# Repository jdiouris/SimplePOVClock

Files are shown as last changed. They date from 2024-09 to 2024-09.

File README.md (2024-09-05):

# Horloge à persistance rétinienne
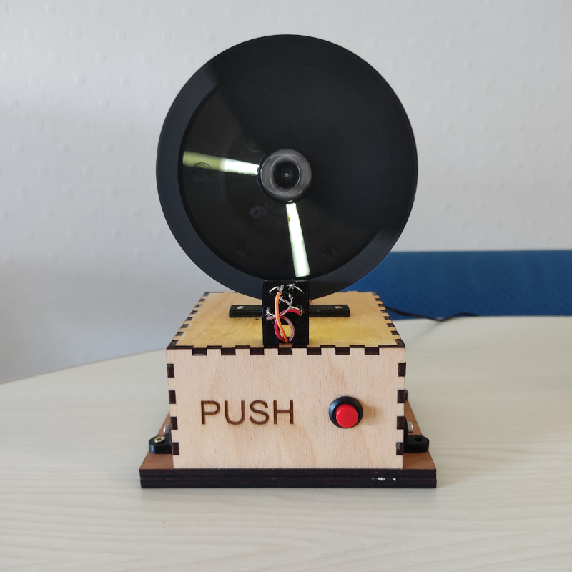
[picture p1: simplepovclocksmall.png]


## Principe
Un disque muni d'une fente tourne sur son axe. Des leds s'allument périodiquement pour visualiser les aiguilles des heures et des minutes. Un bouton poussoir permet de démarrer la rotation ou l'arrêt du disque. Deux boutons poussoirs à l'arrière permettent de régler l'heure et les minutes. L'heure est sauvegardée dans un circuit RTC.

##  Mécanique
Le boitier et le socle sont en contreplaqué 5mm découpé au laser. Les autres pièces sont réalisées en impression 3D.

|Pièce | Fichier source | Fichier de fabrication |
| ---- | --- | --- |
| Boitier | box.lbrn2  | box.dxf |
| Socle (2) | socle.lbrn2  | socle.dxf |
 | Coupelle | coupelle.scad | coupelle.stl |
| Disque | screen3.scad | screen3.stl |
|Support coupelle | supmoteur.scad | sup1.stl |
|Support coupelle | supmoteur.scad | sup2.stl |
|Support coupelle | supmoteur.scad | sup3.stl |
| Support CNY70 | cny70.scad | cny70.stl |
| Attache boite au socle (4) | attache.scad | attache.stl |

## Electronique

Les composants suivants :

| Composant | Quantité |
| --- | --- |
| Arduino uno | 1 |
| CNY70 | 1 |
| BD139 | 2 |
 | MOSFET | 1 |
 |Module horloge DS1302 | 1 |
 |LEDS 10 mm haute luminosité| 10 |
 | Diode 1N4148 | 1 |
 | Condensateur 10uF | 1|
 | Résistances | voir schéma |
 | Boutons poussoirs diamêtre 12.5 mm | 3 |

 Le schéma est détaillé dans le fichier schema.pdf. La pluspart des composants sont montés sur une carte de prototypage shield Arduino. Le capteur optique CNY70 est monté sur le support imprimé en 3d avec les deux résistances associées.

 ## Programme
 Le programme arduino est povc2.ino.

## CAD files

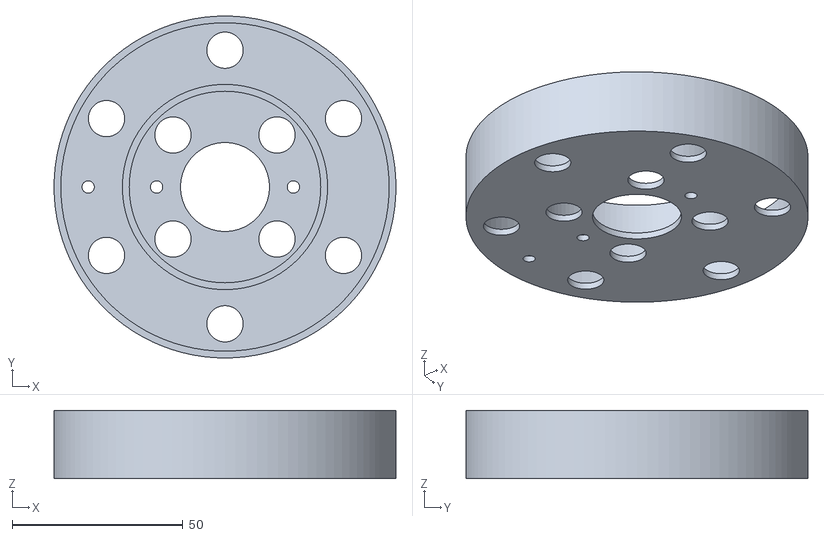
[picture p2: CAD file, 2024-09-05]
coupelle.stl
100.0 x 100.0 x 20.0

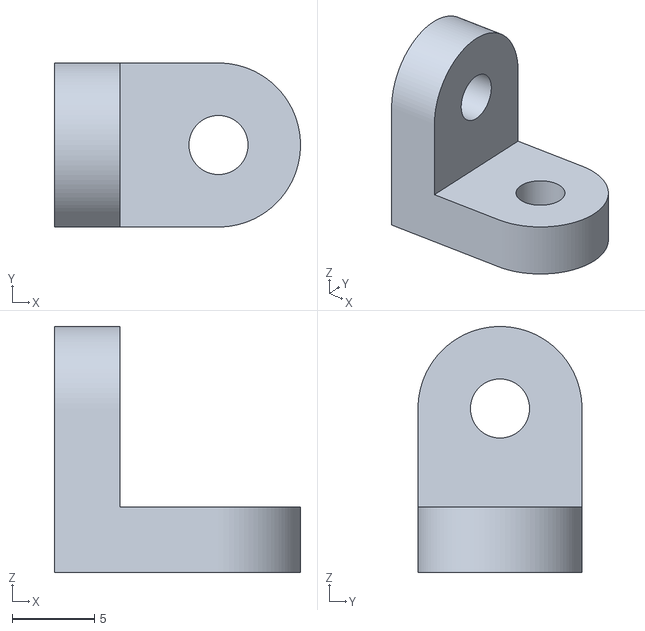
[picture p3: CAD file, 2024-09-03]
attache.stl
15.0 x 10.0 x 15.0

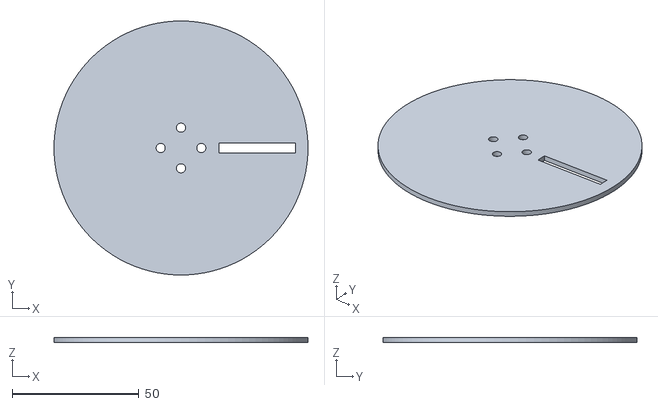
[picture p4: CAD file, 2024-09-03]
screen3.stl
100.0 x 100.0 x 2.00

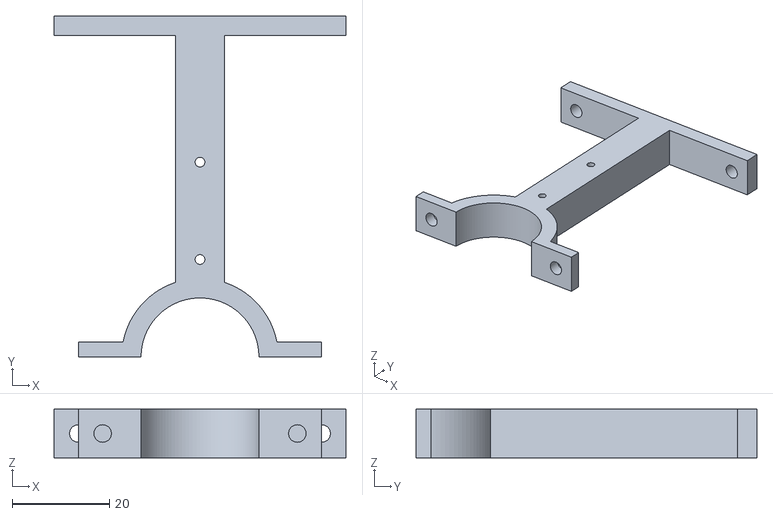
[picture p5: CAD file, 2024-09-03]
sup1.stl
60.0 x 70.0 x 10.0

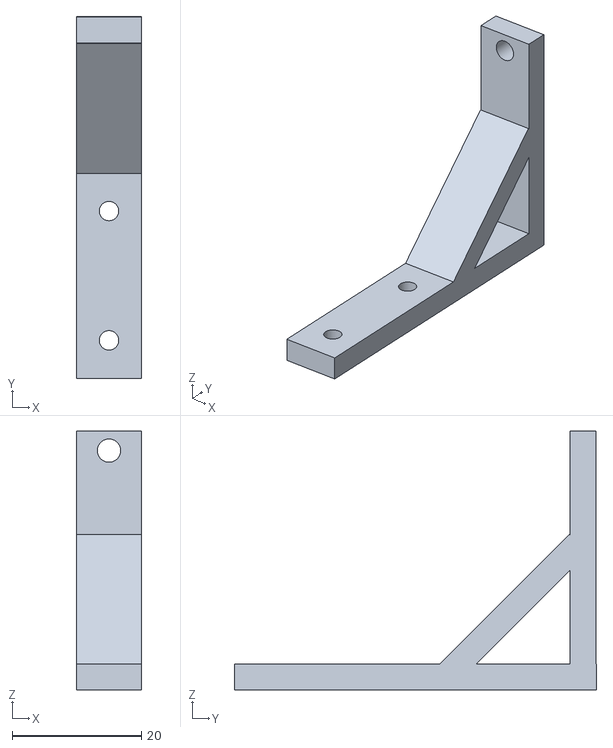
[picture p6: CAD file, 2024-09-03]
sup3.stl
10.0 x 56.0 x 40.0

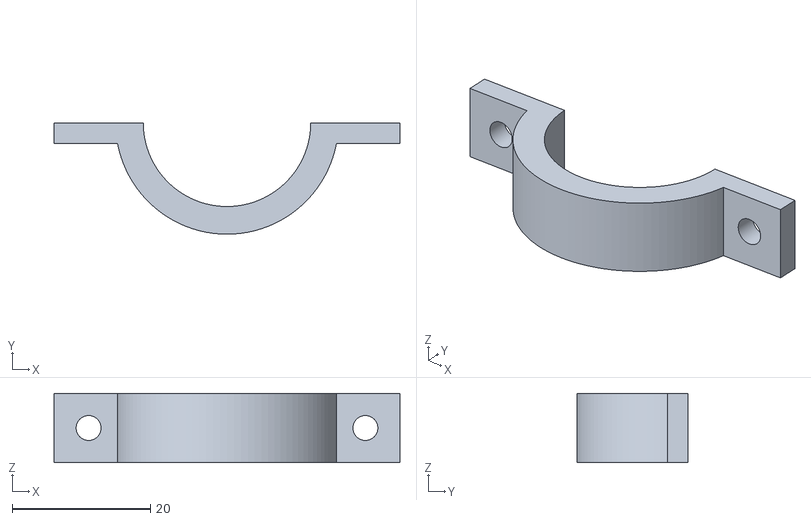
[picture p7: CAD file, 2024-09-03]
sup2.stl
50.0 x 16.1 x 10.0

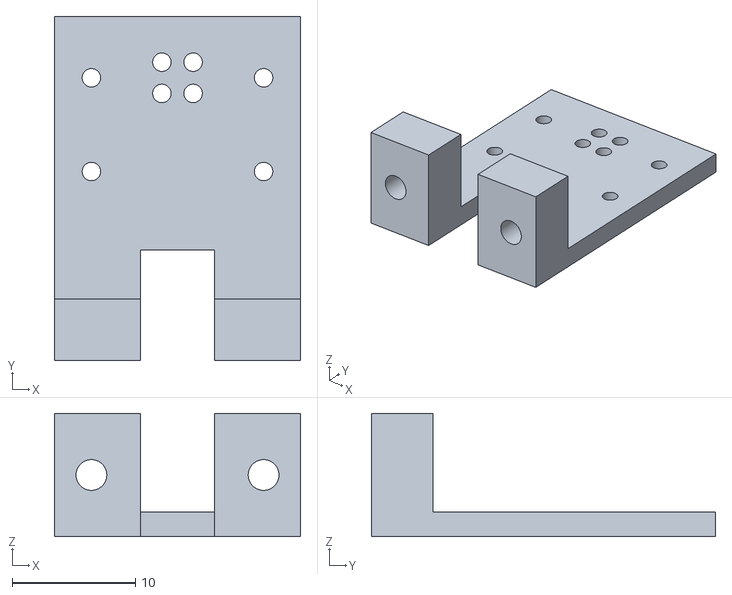
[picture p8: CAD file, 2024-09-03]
cny70.stl
20.0 x 28.0 x 10.0

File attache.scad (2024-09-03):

$fn=100;

H=10;
W=H*1.5;
e=4;

module cote()
{
    difference()
    {
    union()
    {
    cube([e,H,H]);
    translate([0,H/2,H]) rotate([0,90,0]) cylinder(d=H,h=e);
    };
    
     translate([-1,H/2,H]) rotate([0,90,0]) cylinder(d=3.6,h=e+2);
    
}
}

cote();
translate([0,0,e])  rotate([0,90,0]) cote();

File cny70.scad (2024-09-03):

W=20;
Hc=23;
H=Hc+5;
e=2;
w=2.54;
$fn=100;
difference()
{
    union()
    {
    cube([W,H,e]);
    cube([W,5,10]);
    }
    // Cny70
    translate([W/2-w/2,Hc+w/2,-1]) cylinder(d=1.5,h=10);
    translate([W/2+w/2,Hc+w/2,-1]) cylinder(d=1.5,h=10);
    translate([W/2-w/2,Hc-w/2,-1]) cylinder(d=1.5,h=10);
    translate([W/2+w/2,Hc-w/2,-1]) cylinder(d=1.5,h=10);
    // resistance
     translate([3,Hc,-1]) cylinder(d=1.5,h=10);
    translate([3,Hc-3*w,-1]) cylinder(d=1.5,h=10);
    // resistance
     translate([W-3,Hc,-1]) cylinder(d=1.5,h=10);
    translate([W-3,Hc-3*w,-1]) cylinder(d=1.5,h=10);
    // vis
    translate([3,-1,5]) rotate([-90,0,0]) cylinder(d=2.5,h=10);
     translate([W-3,-1,5]) rotate([-90,0,0]) cylinder(d=2.5,h=10);
    // passage
    translate([W/2-3,-1,-1]) cube([6,10,30]);
    
}

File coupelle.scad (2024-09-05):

Dm=26;
D2=100;
D1=60;
e=2;
Dled=10.6;
H=20;

$fn=100;

module anneau(D,e,H)
{
    difference()
    {
        cylinder(h=H,d=D);
    
    // trou moteur
    translate([0,0,-1]) cylinder(h=H+2,d=D-2*e);
    }
}

difference()
{
    union()
    {
    cylinder(h=e,d=D2);
    anneau(D2,2,H);
    anneau(D1,2,H);
    }
    
    // trou moteur
    translate([0,0,-1]) cylinder(h=e+2,d=Dm);
    translate([-20,0,-1]) cylinder(h=e+2,d=3.6);
    translate([+20,0,-1]) cylinder(h=e+2,d=3.6);
    translate([-40,0,-1]) cylinder(h=e+2,d=3.6);
    // trou capteur
    //translate([-D2/2-5,-3.5,H-10]) cube([10,7,20]);
    
    // Leds
    r1=(D1+D2)/4;
    for (a=[0:60:359])
        translate([r1*cos(a+30),r1*sin(a+30),-1]) cylinder(h=e+2,d=Dled);
    r2=(D1+Dm)/4;
    for (b=[0:90:359])
        translate([r2*cos(b+45),r2*sin(b+45),-1]) cylinder(h=e+2,d=Dled);
    
}

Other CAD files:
socle.dxf
box.dxf
screen3.scad
supmoteur.scad

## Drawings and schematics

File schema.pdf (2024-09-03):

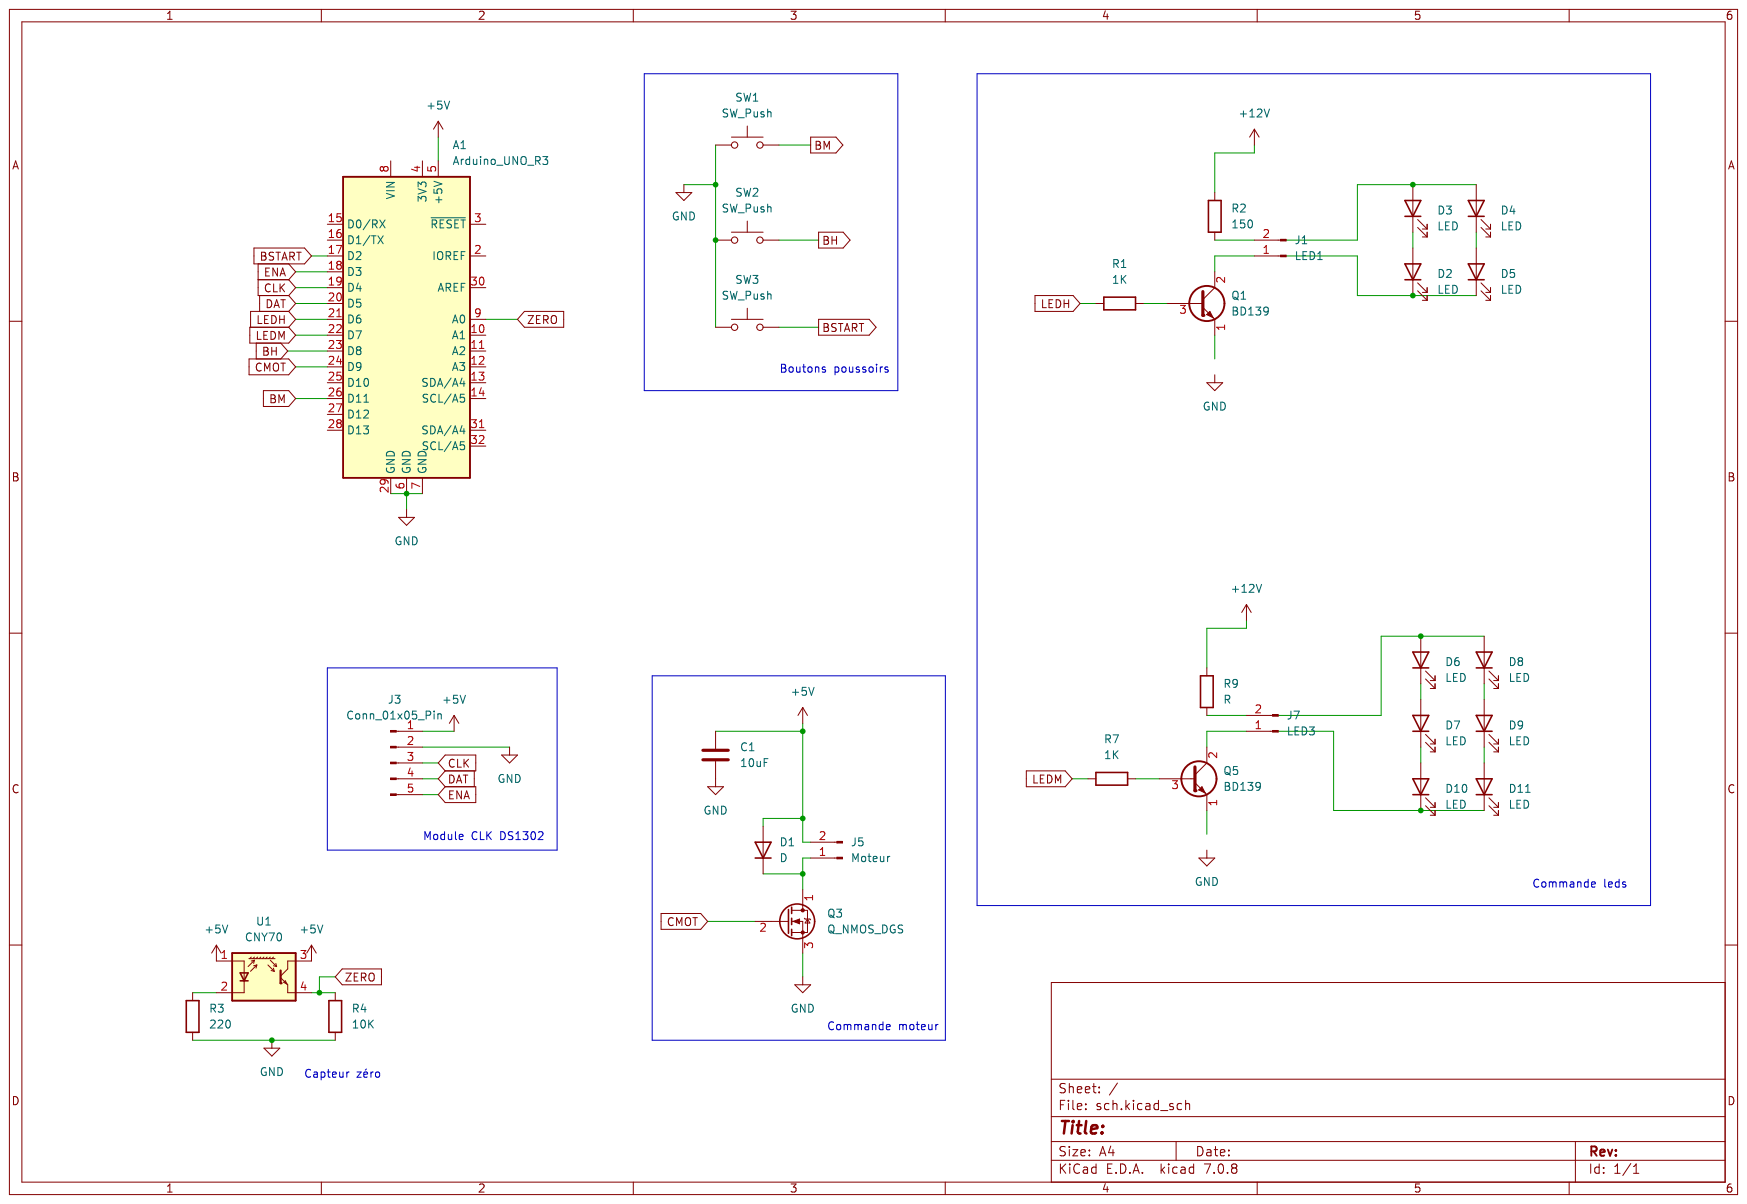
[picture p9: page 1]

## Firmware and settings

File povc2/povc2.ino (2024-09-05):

// ---------------------------------------
//                 POV CLOCK 2                 
//                            (c) JFD 2024
// ---------------------------------------
#include <RtcDS1302.h>
#define PIN_ENA 3
#define PIN_CLK 4
#define PIN_DAT 5

ThreeWire myWire(PIN_DAT,PIN_CLK,PIN_ENA); // IO, SCLK, CE
RtcDS1302<ThreeWire> Rtc(myWire);

#define LEDH 6
#define LEDM 7
#define CMOT 9
#define BM 11
#define BSTART 2
#define BH 8


int h=0;
int m;
int s;
int modifh=0;


int seuil=800;
//unsigned long periode;
float periode=0.0;
unsigned long t1;
unsigned long t2;
unsigned long t0=0;
unsigned long ts;
unsigned long tm;
int run=0;
int speed=50;
int ktours=0;  // Compteur pour lecture périodique de l'heure

// Détermine et affiche la période 
void writePeriode()
{
  periode=0;
   while(analogRead(A0)<seuil);
   while(analogRead(A0)>seuil);
  for (int i=0; i<10; i++)
  {
    t1=millis();
   while(analogRead(A0)<seuil);
   while(analogRead(A0)>seuil);
   periode=periode+(millis()-t1);
   
   digitalWrite(LEDH,HIGH);
   delay(2);
   digitalWrite(LEDH,LOW);
  }
   Serial.print(periode/10);
   Serial.println(" ms");
}

// --------------------------
// Ecrit l'heure dans le RTC
// --------------------------
void setTime(int h,int m, int s)
{
  Serial.print("SetTime");
  Serial.print(h);
  Serial.print(":");
  Serial.println(m);
        RtcDateTime now(24, 8, 17,h, m, s);
        Rtc.SetDateTime(now);
}
// --------------------------
// Lit l'heure dans le RTC
// --------------------------
void getTime()
{
  RtcDateTime now = Rtc.GetDateTime();
   //printDateTime(now);
    h=now.Hour();
    m=now.Minute();
    s=now.Second();

    if (h>12) h=h-12;
}

void mode()
{
  delay(1);  // filtrage parasites...
  if (digitalRead(BSTART)==0)
    switch (run)
    {
      case 0: if ((millis()-ts)>(unsigned long)2000) 
              {
                run=1; 
                analogWrite(CMOT,speed); 
                ts=millis();
                Serial.print(run);
                ktours=600;
              }
              break;
      case 1: if ((millis()-ts)>(unsigned long)2000) 
              {
                run=0; 
                analogWrite(CMOT,0); 
                ts=millis();
                Serial.print(run);
              }
              break;
    }
}

// ------------------
// Initialisations
// ------------------
void setup() 
{
  Rtc.Begin();
  getTime();
  Serial.begin(115200);
  while (!Serial) ;
  pinMode(LEDH,OUTPUT);
  pinMode(LEDM,OUTPUT);
  Serial.println("Start");
  Serial.print(h);
  Serial.print(":");
  Serial.println(m);
  // Commande moteur
   pinMode(CMOT, OUTPUT);
   // Boutons
   pinMode(BM, INPUT_PULLUP);
   pinMode(BH, INPUT_PULLUP);
   pinMode(BSTART, INPUT_PULLUP);

  // ICR1 = 639;     //640 ticks of 16MHz clock == 40uS == 25kHz
  // //OCR1A = 320;    //50% duty cycle
  // TCCR1A = _BV(COM1A1) | _BV(WGM11);
  // TCCR1B = _BV(WGM13) | _BV(WGM12) | _BV(CS10);  
  TCCR1B = TCCR1B & B11111000 | B00000001;
  
  analogWrite(CMOT,0);
  //writePeriode();
  attachInterrupt(digitalPinToInterrupt(BSTART), mode, FALLING);
}

int okh;  // Flag affichage aiguille des heures
int okm;  // Flag affichage aiguille des minutes

int kh=0; // Incrémentation des heures

void loop() 
{
   t0=millis();
   periode=0;
    okh=0;
    okm=0;
    
    if (digitalRead(BM)==0) 
    {
      m++;
      if (m>59) m=0;
      modifh=1;
      tm=millis();
      
    }

    if (digitalRead(BH)==0) 
    {
      kh++;
      if (kh==10)
      {
        kh=0;
      h++;
      if (h>11) h=0;
      modifh=1;
      tm=millis();
      }
      
    }
   while(analogRead(A0)>seuil);

   while(analogRead(A0)<seuil)
   {
      if ((millis()-t0)>t1)
      {
        if (okh==0)
        {
          digitalWrite(LEDH,HIGH);
          delay(1);
          digitalWrite(LEDH,LOW);
          okh=1;
        }

      }
      if ((millis()-t0)>t2)
      {
        if (okm==0)
        {
          digitalWrite(LEDM,HIGH);
          digitalWrite(LEDH,HIGH);
          delay(1);
          digitalWrite(LEDM,LOW);
          digitalWrite(LEDH,LOW);
          okm=1;
        }

        if (modifh==1) if ((millis()-tm)>1000) { setTime(h,m,0); modifh=0; }
        
      }
   }
   //periode=periode*0.5+(millis()-t1)*0.5;
   periode=(millis()-t0);
   t1=int(periode*(h+6+m/60.0)/12);
   if (t1>=periode) t1-=periode;
   t2=int(periode*(m+30)/60);
   if (t2>=periode) t2-=periode;

   if (t1>periode) t1-=periode;
   ktours++;
   if (ktours>600)
   {
    ktours=0;
    if (modifh==1) { setTime(h,m,0); modifh=0; }

    getTime();
    // Serial.print(h);
    // Serial.print(":");
    // Serial.println(m);
    // Serial.println(periode);

   }
}
